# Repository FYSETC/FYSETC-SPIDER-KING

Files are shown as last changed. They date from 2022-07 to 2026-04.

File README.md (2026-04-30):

# FYSETC-SPIDER-KING

## 1. Product introduction

10 axis industrial grade 3D printer motherboard

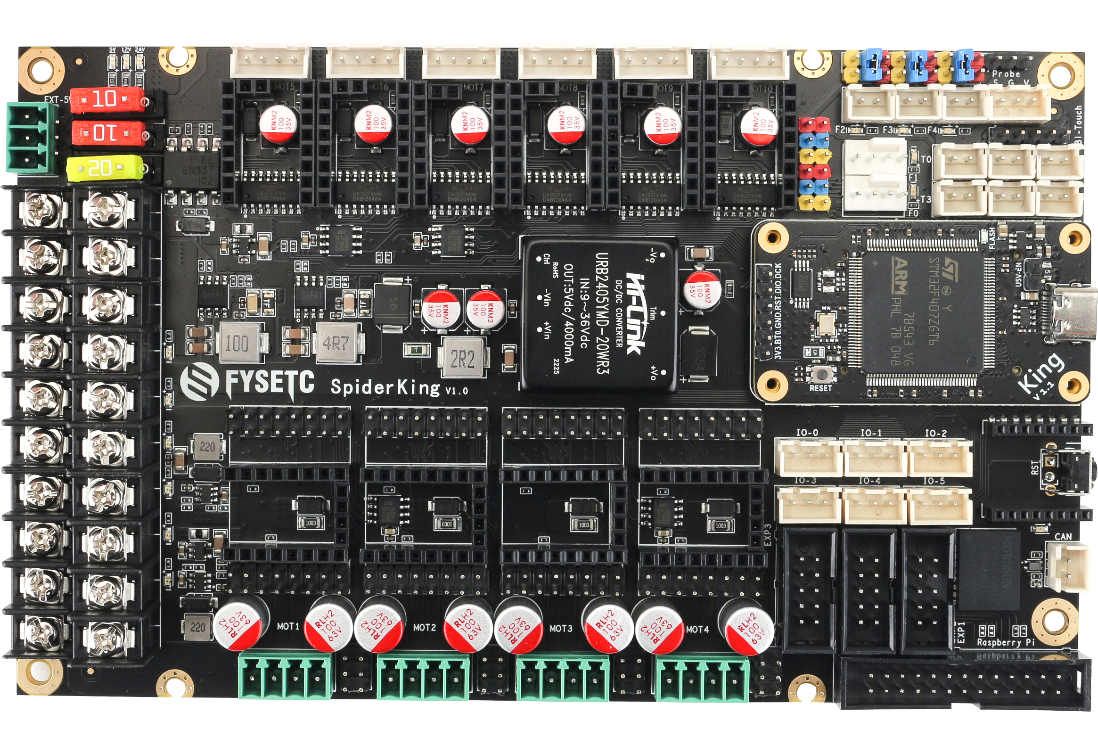
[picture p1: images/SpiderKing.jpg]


### 1.1 Advantage

1. Replaceable control core:
   It has a replaceable control core(Named 'King' core).You can freely choose between 4xRP2040(King-R) / STM32F446(King-446) / STM32F407(King-407) / STM32H7XX(King-H7xx), and even you can make your own control core(We will open source the interface).

2. Intelligent identification of stepper driver type:
   With an additional MCU, Spider-King can identify the driver type and switch the SPI/UART channel automatically.
   This feature save you time on searching doc of how to set the jumppers, keep you away from borning setting jumppers. No longer has problems with stepper driver setting. (If you want to use this feature, you need our new stepper driver)

3. Multiple firmware support:
   It supports multiple firmwares.You can choose to use Klipper / Marlin 2.0 / Reprap Firmware / GRBL and other firmware according to your preferences and needs.

4. Industrial-grade standard design, 5000V full IO isolation:
   It provides a more secure hardware base: equiped with onboard high-power isolated power supply, and the control core is isolated from all high-voltage peripherals, including stepper motor drive, MOSFET output, high-voltage input signal, CAN bus, etc.

5. 10 way stepper motor drive support:
   Onboard 10 way stepping motor drive socket, 6x 3A max (maximum 35V), 4x 6A max (maximum 55V). Any socket supports SPI / UART / standalone mode.It has a new 6A drive design. It can drive 57 or even 86 step motors without external drive;

6. A variety of communication interfaces support:
   It supports onboard 5000V isolated CAN interface, supports wireless WI-FI interface, supports ESP32 high-speed communication module, supports multiple connection to Raspberry Pi, including UART, SPI and USB.

7. Centralized heat dissipation of heat-generating components:
   We centralized most heating components like 5V power supply, stepper driver in the middle area of the board, this area can be covered with the 12CM fan for cooling. You don't need to rack your brains to design the air duct, you can get better and more stable output performance.

8. Compatible with RRF firmware standard socket design:
   The socket layout is set according to Duet wiring and layout, which is more convenient to use the RRF. And more, we adds two DUET type fan ports which have feedback signal.

9. All Solid Capacitors: Power Section：
   It can provide more stable power supply and higher efficiency.

10. Compact Design:
    It has a very small size of 177mm*108mm, realizes multiple MOSFET outputs, and supports up to 10 stepper drivers.

## 2. Documents

Check our wiki [FYSETC SPIDER KING - FYSETC WIKI](https://wiki.fysetc.com/docs/FYSETCSPIDERKING).

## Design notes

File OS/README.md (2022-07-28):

# OS

## SAMFi-OS_OrangePi_zero

Before you use the [SAMF-OS_OrangePi_zero](https://github.com/FYSETC/FYSETC-SAMFi-OS). You need an TF card with at least 8G capacity. 

### Step 1

Download and flash the OS image with `balenaEtcher` software to your TF card. Insert your flashed TF card to OrangePi-zero and connect Ethernet cable then power on. Find the ip address of OrangePi-zero on your router, host name is `orangepizero`.

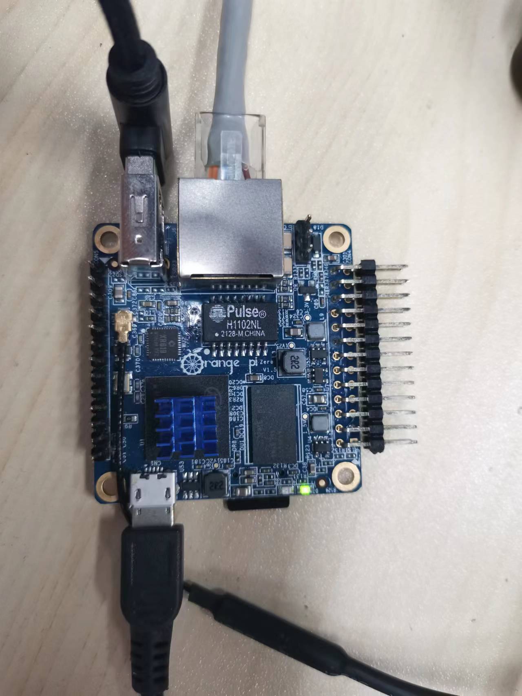
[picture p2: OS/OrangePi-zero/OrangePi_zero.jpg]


### Step 2

You can find the firmware `klipper.bin` in `OrangePi-zero` folder after you download the github repository. It is also stay in the OS path `firmwares\spider-king407.bin` after you login the OS with SSH.

Original SSH account and password:

```
account: fysetc
password: fysetc123
```

Enter DFU mode(set a jumper on `3.3V` and `BT0` pin on king core board and click the reset button, you need power on the board with 24v ), and flash the firmware with the command below after you connect your OrangePi and Spider-king with USB cable.

```
dfu-util -R -a 0 -s 0x08008000:leave -D firmwares/spider-king407.bin
```

or follow the instructions [here](https://github.com/FYSETC/FYSETC-SPIDER#44--firmware-upload) for firmware uploading. Remember to remove the `3.3v` `BT0` jumper and click the reset button after you flashed the firmware. 

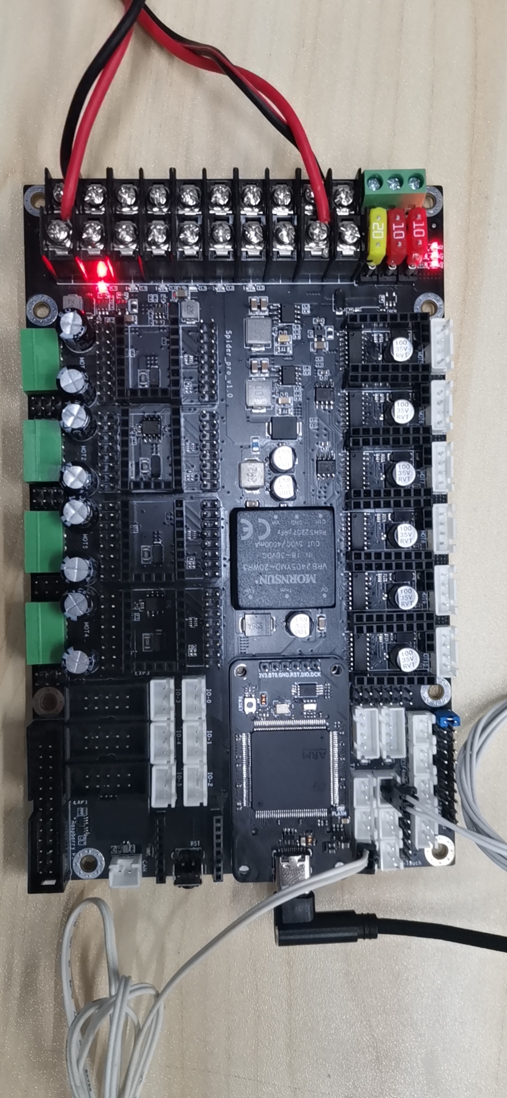
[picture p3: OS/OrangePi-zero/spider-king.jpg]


### Step 3:

Prepare the `pinter.cfg`, using the command below

```
cp klipper_config/spider-king.cfg klipper_config/printer.cfg
```

You probably need to change `id` by `ls /dev/serial/by-id` command.

I use the voron2.4 config for this example, you need to change it according to your machine. Now visit the webpage with your orangepi-zero IP address. Good to go.

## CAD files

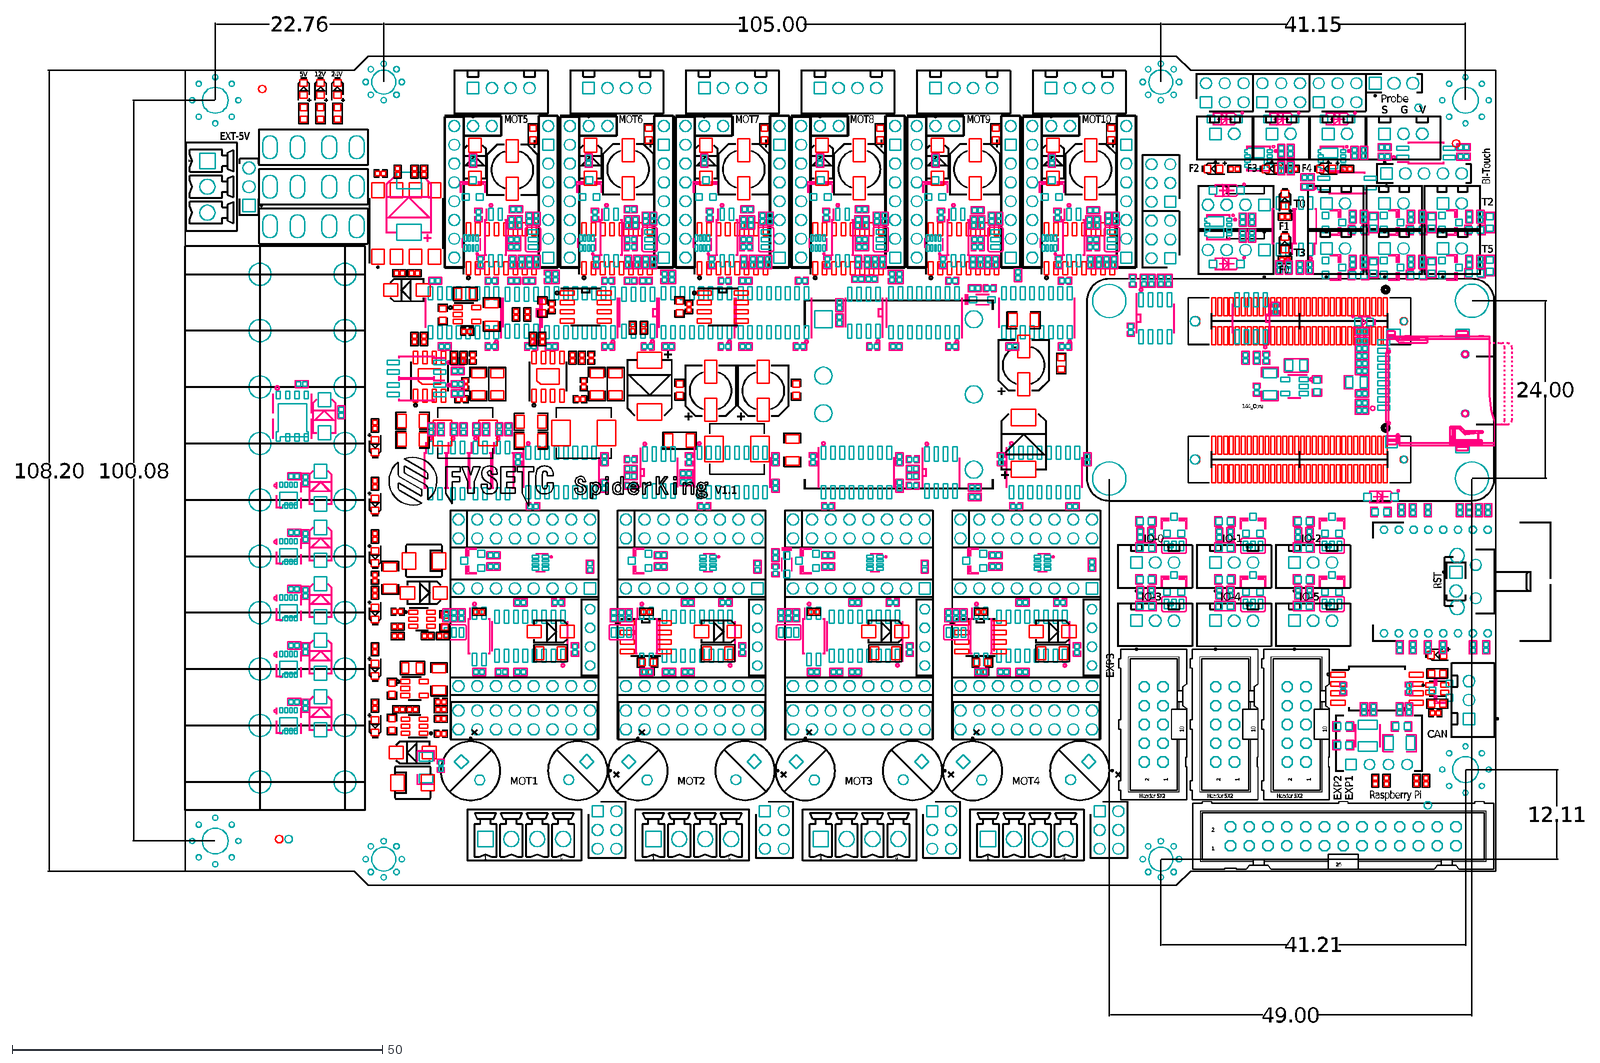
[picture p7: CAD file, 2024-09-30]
hardware/Spider_King v1.1_CAD.dxf
144_Core
1
4
26
2
10
Header 5X2
V1.1
EXT-5V
V
S
G
Probe
24V
12V
5V
RST
Bl-Touch
F4
F3
F2
F1
F0
Raspberry Pi
IO-0
T5
T3
T2
T0
IO-5
IO-4
IO-3
IO-2
IO-1
CAN
EXP2
EXP1
EXP3
MOT10
MOT9
MOT8
MOT7
MOT6
MOT5
MOT4
MOT3
MOT2
MOT1
100.08
108.20
105.00
41.15
24.00
22.76
12.11
41.21
49.00

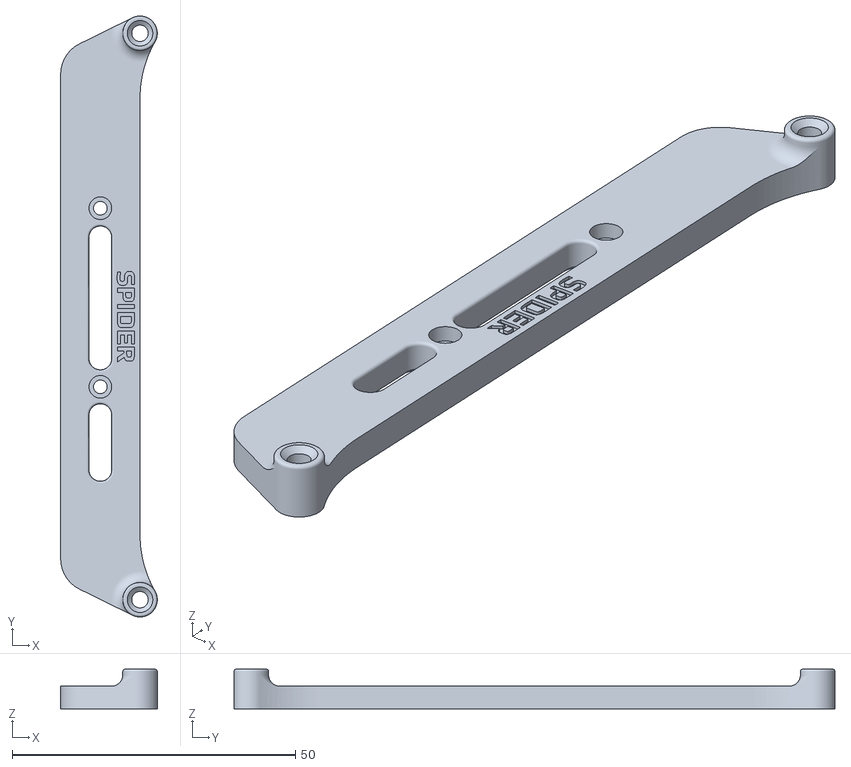
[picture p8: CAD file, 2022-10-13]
STLs/Holder_long_right.STL
17.1 x 106.0 x 7.00

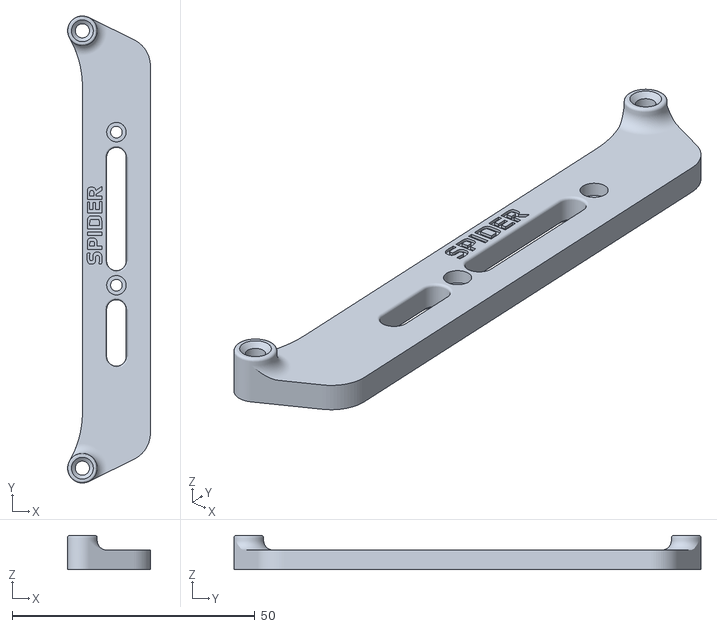
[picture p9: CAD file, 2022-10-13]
STLs/Holder_short_left.STL
17.1 x 96.1 x 7.00

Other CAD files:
hardware/Spider_King_CAD.dxf

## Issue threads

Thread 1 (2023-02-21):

TMC5160 Drivers Not detected

benagricola, 2023-02-21:
Using the example Klipper configs, as well as RRF, my SPIDER KING won't detect the BIG-5160 drivers I have installed in my board.

Klipper reports:

```
INFO:root:TMC stepper_x failed to init: Unable to write tmc spi 'stepper_x' register GLOBALSCALER
INFO:root:TMC stepper_y failed to init: Unable to write tmc spi 'stepper_y' register GLOBALSCALER
INFO:root:TMC stepper_z failed to init: Unable to write tmc spi 'stepper_z' register GLOBALSCALER
```

And RRF reports all drivers not present.

Additionally, the example Klipper configuration pins don't match the Pinout diagram in this repo, so I have no idea which pins are the correct ones.

The example Klipper config I'm using is this (using the pin layout from the PDF file in this repo).

```
[mcu]
serial: /dev/serial/by-id/usb-Klipper_stm32f407xx_260035001147393532373434-if00
restart_method: command

[stepper_x]
step_pin: PG7
dir_pin: PG6
enable_pin: PE11
rotation_distance: 40
microsteps: 16
full_steps_per_rotation:200
endstop_pin: tmc5160_stepper_x:virtual_endstop
position_min: 0
position_endstop: 0
position_max: 235
homing_speed: 35
homing_retract_dist: 5
#homing_positive_dir: true

[tmc5160 stepper_x]
## Soft SPI
spi_software_mosi_pin: PE14
spi_software_miso_pin: PE13
spi_software_sclk_pin: PE12
cs_pin: PD2
diag0_pin: !PF6
interpolate: False
run_current: 0.8
#hold_current: 0.5
stealthchop_threshold: 0
sense_resistor: 0.075
driver_SGT: 1

[stepper_y]
step_pin: PG14
dir_pin: PG12
enable_pin: PG15
microsteps: 16
rotation_distance: 40
full_steps_per_rotation: 200
endstop_pin: tmc5160_stepper_y:virtual_endstop
position_min: 0
position_endstop: 0
position_max: 235
homing_speed: 35
homing_retract_dist: 5

[tmc5160 stepper_y]
## Soft SPI
spi_software_mosi_pin: PE14
spi_software_miso_pin: PE13
spi_software_sclk_pin: PE12
cs_pin: PD8
diag0_pin: !PF8
interpolate: False   #true   False
run_current: 0.8
#hold_current: 0.5
stealthchop_threshold: 0
sense_resistor: 0.075
driver_SGT: 1

#####################################################################
#   Z Motor
#####################################################################

[stepper_z]
step_pin: PD4
dir_pin: PD6
enable_pin: PD5
rotation_distance: 8
gear_ratio: 40:16
microsteps: 256
endstop_pin: tmc5160_stepper_z:virtual_endstop
position_endstop: 0
position_max: 235
position_min: 0
homing_speed: 7
second_homing_speed: 3
homing_retract_dist: 3

[tmc5160 stepper_z]
spi_software_mosi_pin: PE14
spi_software_miso_pin: PE13
spi_software_sclk_pin: PE12
cs_pin: PD7
diag0_pin: !PF11
interpolate: False   #true
run_current: 0.7
hold_current: 0.4
sense_resistor: 0.110
stealthchop_threshold: 0

[printer]
kinematics: cartesian
max_velocity: 200
max_accel: 1500
max_z_velocity: 10
max_z_accel: 100
square_corner_velocity: 4.0
```

Big5160 boards are installed in the orientation from the WIKI - With the BIG-5160 text upside-down when looking at the board from the high voltage motor connectors.

Please help work out what's wrong here, because the board won't work without drivers :)

benagricola, 2023-02-22:
For anyone else finding this:

The BIG5160 drivers specifically need power on the `48V-PWR` rail _as well as_ whatever you have on `PWE-IN`. You can run 24v to both of these and the drivers will work fine, but you have to have _both_ connected up, as `PWE-IN` does not provider power to the "High Voltage" motor drivers.

The configuration which worked great for me with standard currents (not tuned yet) is:

```
[mcu]
serial: /dev/serial/by-id/usb-Klipper_stm32f407xx_260035001147393532373434-if00
restart_method: command

[stepper_x]
step_pin: PG7
dir_pin: PG6
enable_pin: !PE11
microsteps: 16
rotation_distance: 40
full_steps_per_rotation: 200
endstop_pin: !PC5
position_min: 0
position_endstop: 0
position_max: 235
homing_speed: 35
homing_retract_dist: 5

[tmc5160 stepper_x]
## Soft SPI
spi_software_mosi_pin: PE14
spi_software_miso_pin: PE13
spi_software_sclk_pin: PE12
cs_pin: PD2
diag1_pin: PF6
interpolate: False   #true   False
run_current: 0.8
#hold_current: 0.5
stealthchop_threshold: 0
sense_resistor: 0.075
driver_SGT: -64

[stepper_y]
step_pin: PG14
dir_pin: PG12
enable_pin: !PG15
microsteps: 16
rotation_distance: 40
full_steps_per_rotation: 200
endstop_pin: !PC4
position_min: 0
position_endstop: 0
position_max: 235
homing_speed: 35
homing_retract_dist: 5

[tmc5160 stepper_y]
## Soft SPI
spi_software_mosi_pin: PE14
spi_software_miso_pin: PE13
spi_software_sclk_pin: PE12
cs_pin: PD8
diag1_pin: PF8
interpolate: False   #true   False
run_current: 0.8
#hold_current: 0.5
stealthchop_threshold: 0
sense_resistor: 0.075
driver_SGT: -64

#####################################################################
#   Z Motor
#####################################################################

[stepper_z]
step_pin: PD4
dir_pin: PD6
enable_pin: !PD5
rotation_distance: 8
gear_ratio: 40:16
microsteps: 256
endstop_pin: !PB6
position_endstop: 0
position_max: 235
position_min: 0
homing_speed: 7
second_homing_speed: 3
homing_retract_dist: 3

[tmc5160 stepper_z]
spi_software_mosi_pin: PE14
spi_software_miso_pin: PE13
spi_software_sclk_pin: PE12
cs_pin: PD7
diag1_pin: PF11
interpolate: False   #true
run_current: 0.7
hold_current: 0.4
sense_resistor: 0.075
stealthchop_threshold: 0
sense_resistor: 0.075
driver_SGT: -64

[printer]
kinematics: cartesian
max_velocity: 200
max_accel: 1500
max_z_velocity: 10
max_z_accel: 100

[display_status]
[pause_resume]
[virtual_sdcard]
path = /home/bagricola/klipper/blah

[board_pins]
aliases:
    # EXP1 header
    EXP1_1=PC9, EXP1_3=PC12, EXP1_5=PC10, EXP1_7=PG4, EXP1_9=<GND>,
    EXP1_2=PA8, EXP1_4=PD0, EXP1_6=PC11, EXP1_8=PE7, EXP1_10=<5V>,
    # EXP2 header
    EXP2_1=PA6, EXP2_3=PC6, EXP2_5=PC7, EXP2_7=PB10,  EXP2_9=<GND>,
    EXP2_2=PA5, EXP2_4=PA4, EXP2_6=PA7, EXP2_8=<RST>, EXP2_10=<5V>,

[display]
lcd_type: uc1701
cs_pin: EXP1_3
a0_pin: EXP1_4
rst_pin: EXP1_5
contrast: 63
encoder_pins: ^EXP2_5, ^EXP2_3
click_pin: ^!EXP1_2
spi_software_miso_pin: EXP2_1
spi_software_mosi_pin: EXP2_6
spi_software_sclk_pin: EXP2_2

[output_pin beeper]
pin: EXP1_1

[neopixel fysetc_mini12864]
pin: EXP1_6
chain_count: 3
color_order: RGB
initial_RED: 0.4
initial_GREEN: 0.4
initial_BLUE: 0.4

[delayed_gcode setdisplayneopixel]
initial_duration: 1
gcode:
        SET_LED LED=fysetc_mini12864 RED=1 GREEN=1 BLUE=1 INDEX=1 TRANSMIT=0
        SET_LED LED=fysetc_mini12864 RED=1 GREEN=0 BLUE=0 INDEX=2 TRANSMIT=0
        SET_LED LED=fysetc_mini12864 RED=1 GREEN=0 BLUE=0 INDEX=3

[menu]

[gcode_button emergency_stop]
pin: !PF14
press_gcode:
    M117 "Emergency Stop Pressed!"
    SET_LED LED=fysetc_mini12864 RED=1 GREEN=0 BLUE=0 INDEX=1
    M112
```

This is using BIG5160 drivers in the 1, 2 and 4 motor positions, X,Y and Z endstops in IO0, IO1 and IO2, the LED + RGB screen plugged into `EXP1` and `EXP2`, and a normally-closed e-stop button on IO5.

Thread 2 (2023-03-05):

STM32F407 not accepting firmware.bin files or showing USB-serial connection

dmason1992, 2023-03-05:
I have been trying to get [Remora](https://github.com/scottalford75/Remora) installed on the Spider King board.

Unfortunately during my trials the board has stopped responding to firmware. I am able to connect via DFU when BT0 is jumped to 3v3 pin so I can upload new firmware via the STM32Cube programmer software.

Can you provide the standard bootloader to get it back to factory state and for firmware to work via SD card upload.

Note - possibly unrelated but the USB serial does not work right now and a device only connects to the PC when the BT0 jumper is added and the board is reset.

dmason1992, 2023-04-28:
Fixed by flashing factory firmware for STM chip via USB option

Closed 2023-04-28.

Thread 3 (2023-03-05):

Add Remora for Linux CNC support

dmason1992, 2023-03-05:
Hi,

The high current drivers on this board make it a great candidate for CNC machine control however I would like to use LinuxCNC which required Remora (https://github.com/scottalford75/Remora) to be run on the board.

Please can you add remora bin + config files?

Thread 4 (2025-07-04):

All tmc 2209 on error: Unable to read tmc uart 'stepper_z1' register GCONF

mrtian, 2025-07-04:
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

**I put my tmc 2209 to BTT ,it's work fine.**

my printer config:

## In MOT5 Position
## Z0 Stepper - Front Left
[stepper_z]
step_pin: PE5
dir_pin: PC13
enable_pin: !PE6
microsteps: 16
rotation_distance: 2 #与丝杠导程数一致
full_steps_per_rotation: 200
gear_ratio: 40:16
microsteps: 256
##  In IO-2 Position
endstop_pin: ^PB6
##  Z-position of nozzle (in mm) to z-endstop trigger point relative to print surface (Z0)
##  (+) value = endstop above Z0, (-) value = endstop below
##  Increasing position_endstop brings nozzle closer to the bed
##  After you run Z_ENDSTOP_CALIBRATE, position_endstop will be stored at the very end of your config
position_endstop: 0
position_max: 300
position_min: -3
homing_speed: 6
second_homing_speed: 3
homing_retract_dist: 3

##  Make sure to update below for your relevant driver (2208 or 2209)
[tmc2209 stepper_z]
uart_pin: PC14
uart_address: 0
interpolate: True
run_current: 0.8
hold_current: 0.5
stealthchop_threshold: 0

##  In MOT6 Position
##  Z1 Stepper Rear Center
[stepper_z1]
step_pin: PE3
dir_pin: !PE4
enable_pin: !PE2
microsteps: 16
rotation_distance: 2
full_steps_per_rotation: 200

##  Make sure to update below for your relevant driver (2208 or 2209)
[tmc2209 stepper_z1]
uart_pin: PC15
uart_address: 0
interpolate: True
run_current: 0.8
hold_current: 0.5
sense_resistor: 0.110
stealthchop_threshold: 0

##  In MOT7 Position
##  Z2 Stepper - Front Right
[stepper_z2]
step_pin: PG13
dir_pin: PG8
enable_pin: !PG9
microsteps: 16
rotation_distance: 2
full_steps_per_rotation: 200

##  Make sure to update below for your relevant driver (2208 or 2209)
[tmc2209 stepper_z2]
uart_pin: PG3
uart_address: 0
interpolate: True
run_current: 0.8
hold_current: 0.5
sense_resistor: 0.110
stealthchop_threshold: 0

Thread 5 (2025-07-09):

说好几年了，这个接口在哪里能找到？

mrtian, 2025-07-09:
Replaceable control core: It has a replaceable control core(Named 'King' core).You can freely choose between 4xRP2040(King-R) / STM32F446(King-446) / STM32F407(King-407) / STM32H7XX(King-H7xx), and even you can make your own control core(We will open source the interface).

说好几年了，这个接口在哪里能找到？

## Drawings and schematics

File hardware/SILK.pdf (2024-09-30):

# ART FILM - adt

# EXT-5V

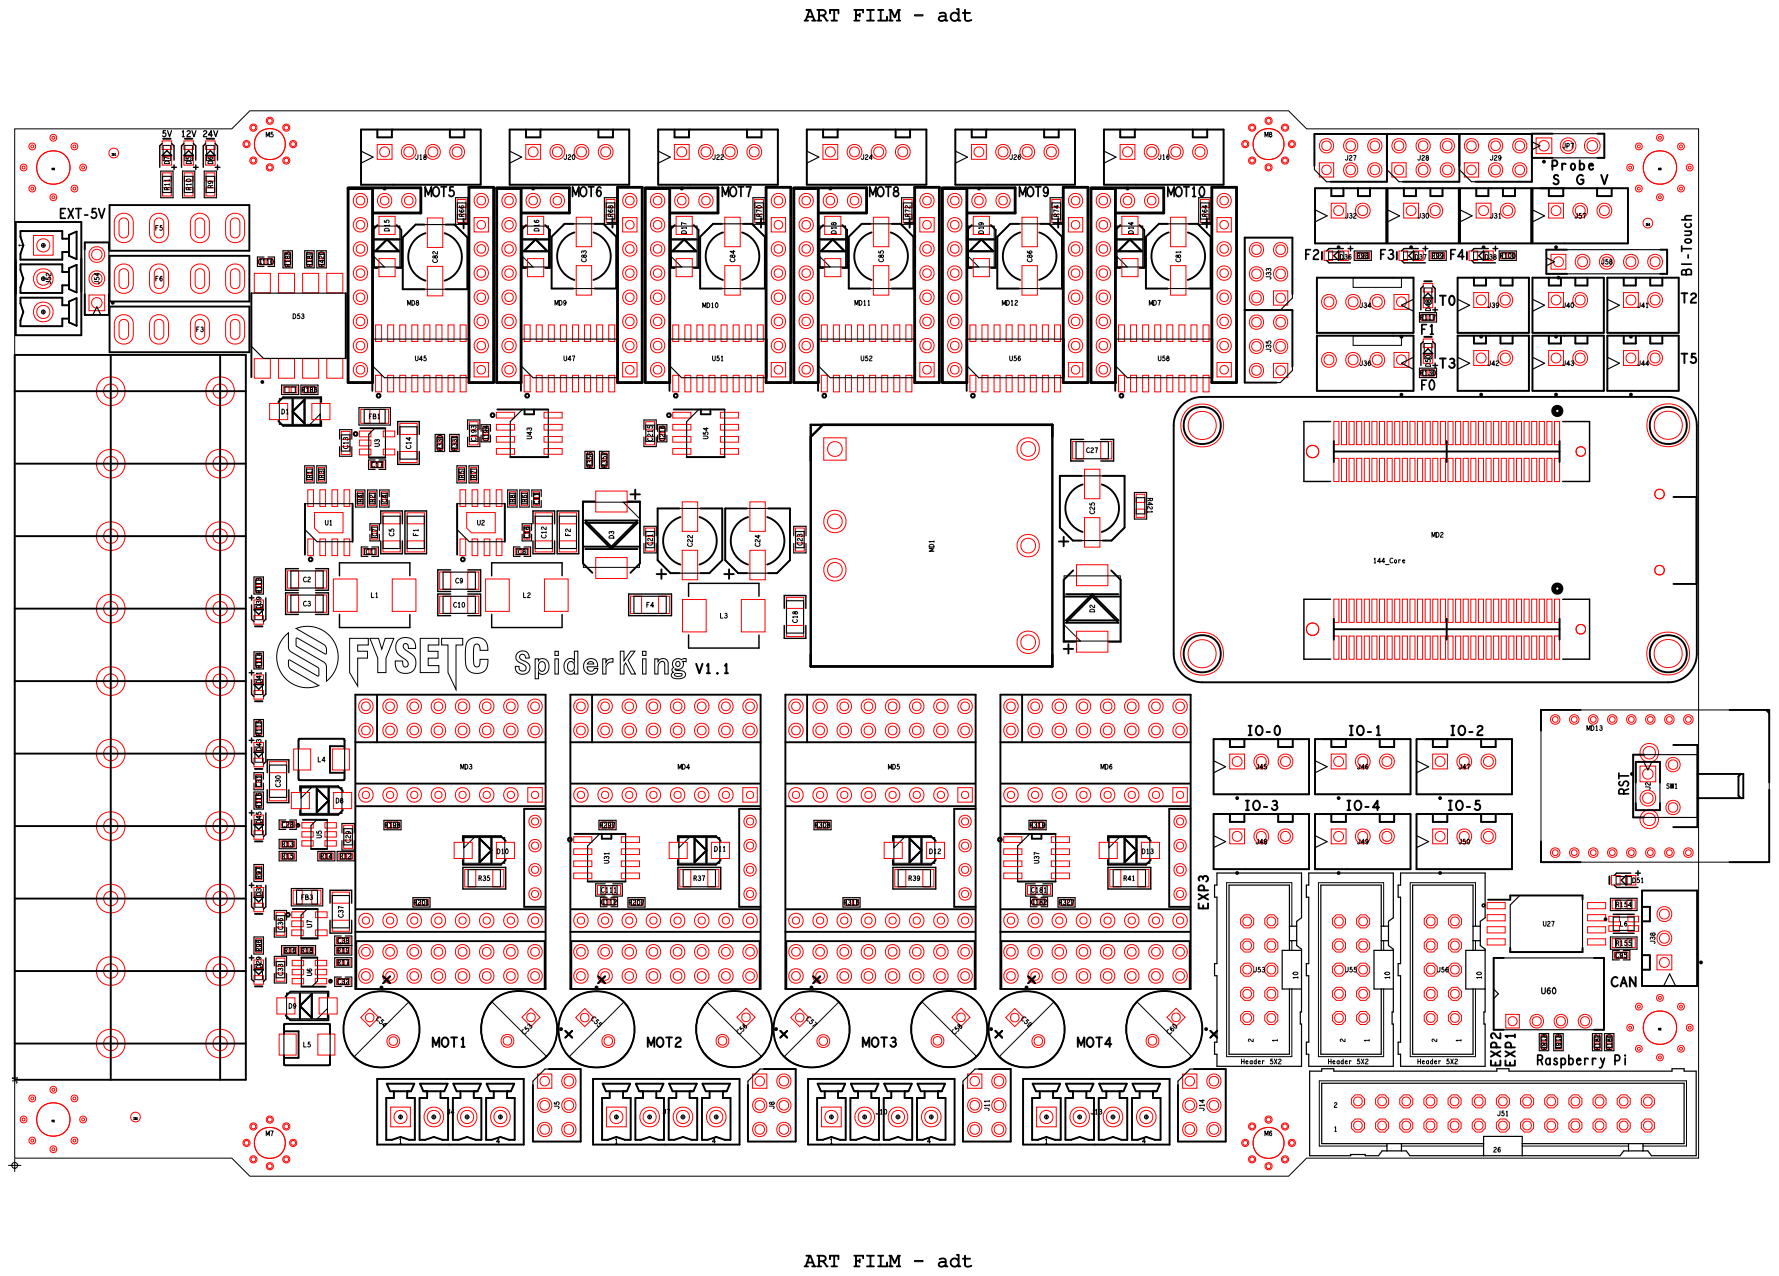
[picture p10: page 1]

# ART FILM - adb

5V

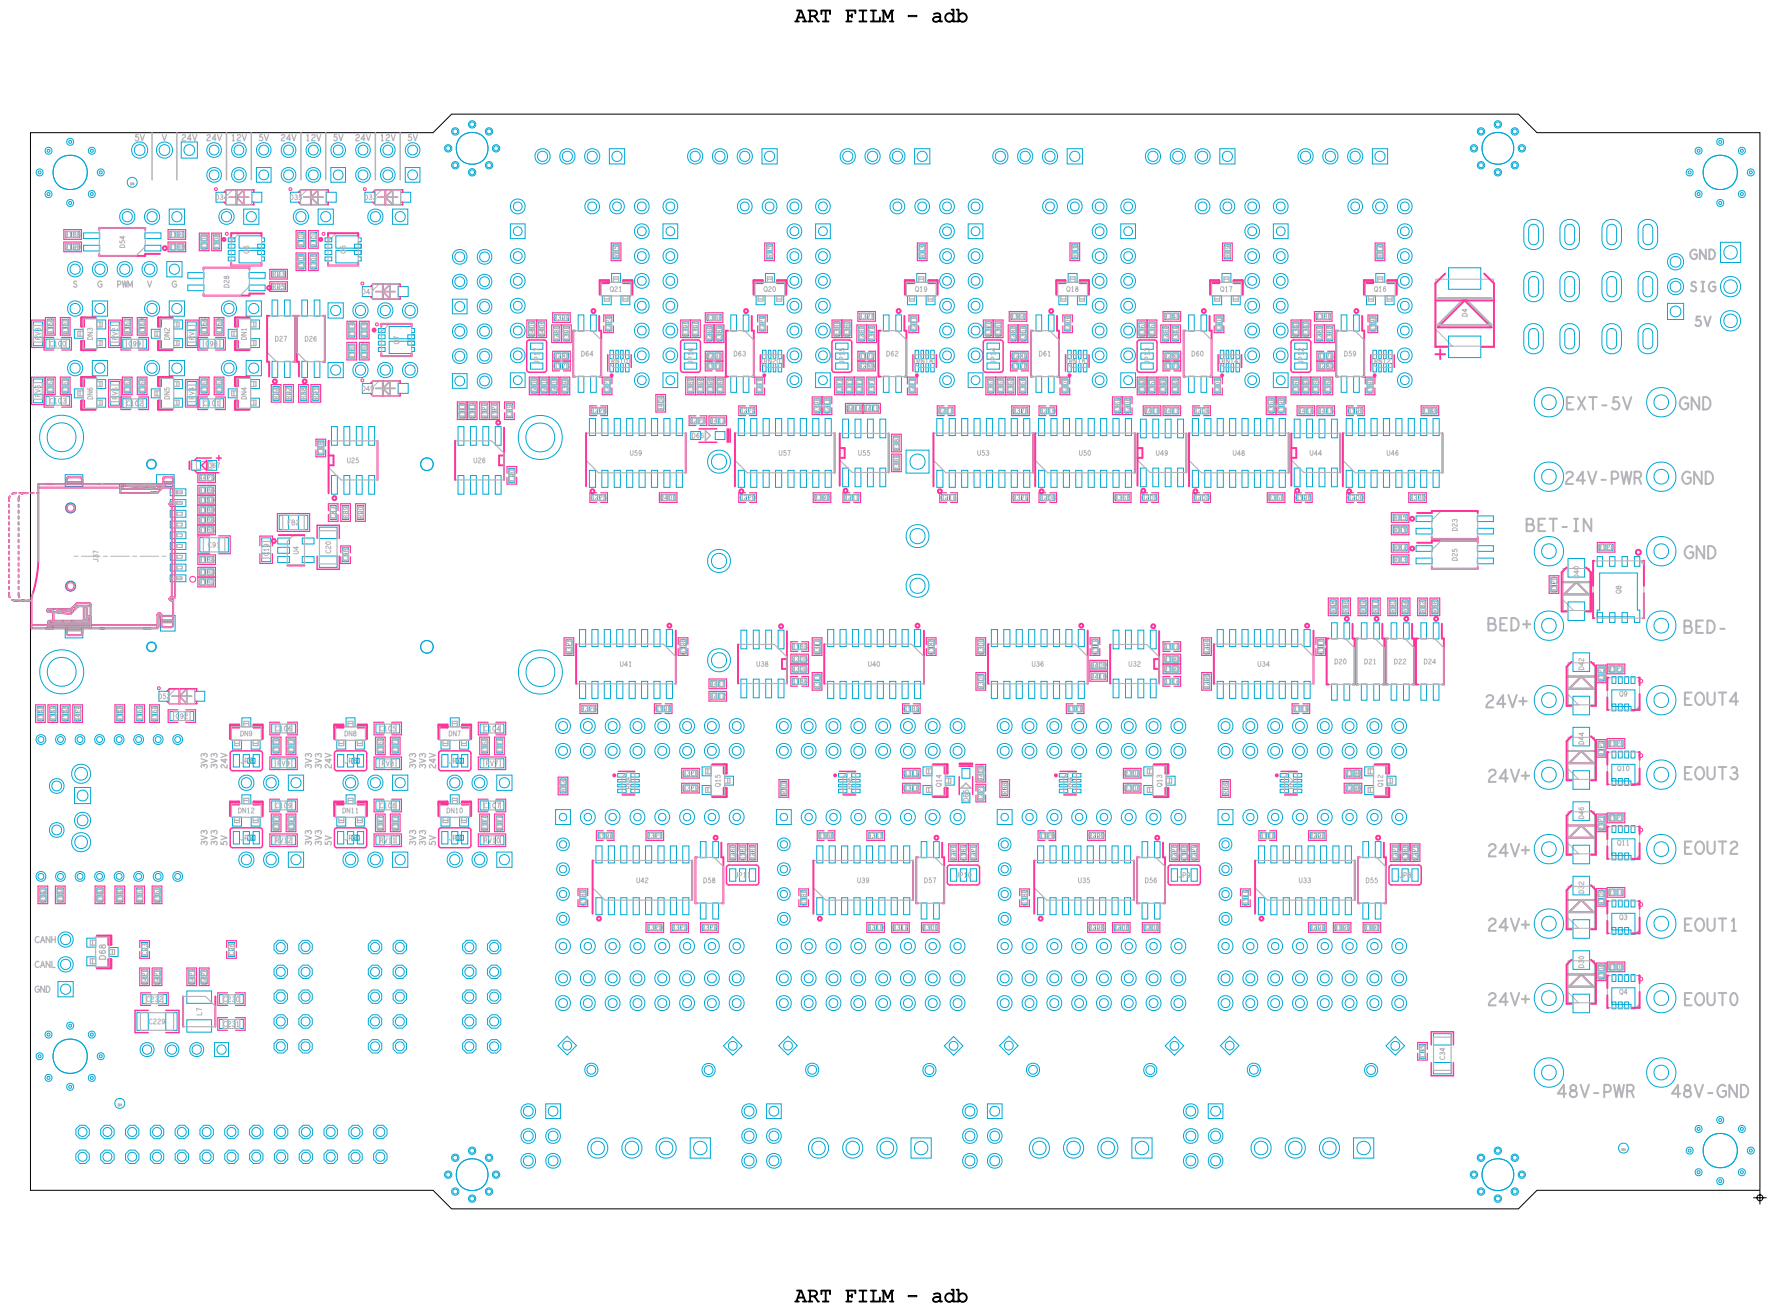
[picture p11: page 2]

# ART FILM - silktop

# EXT-5V

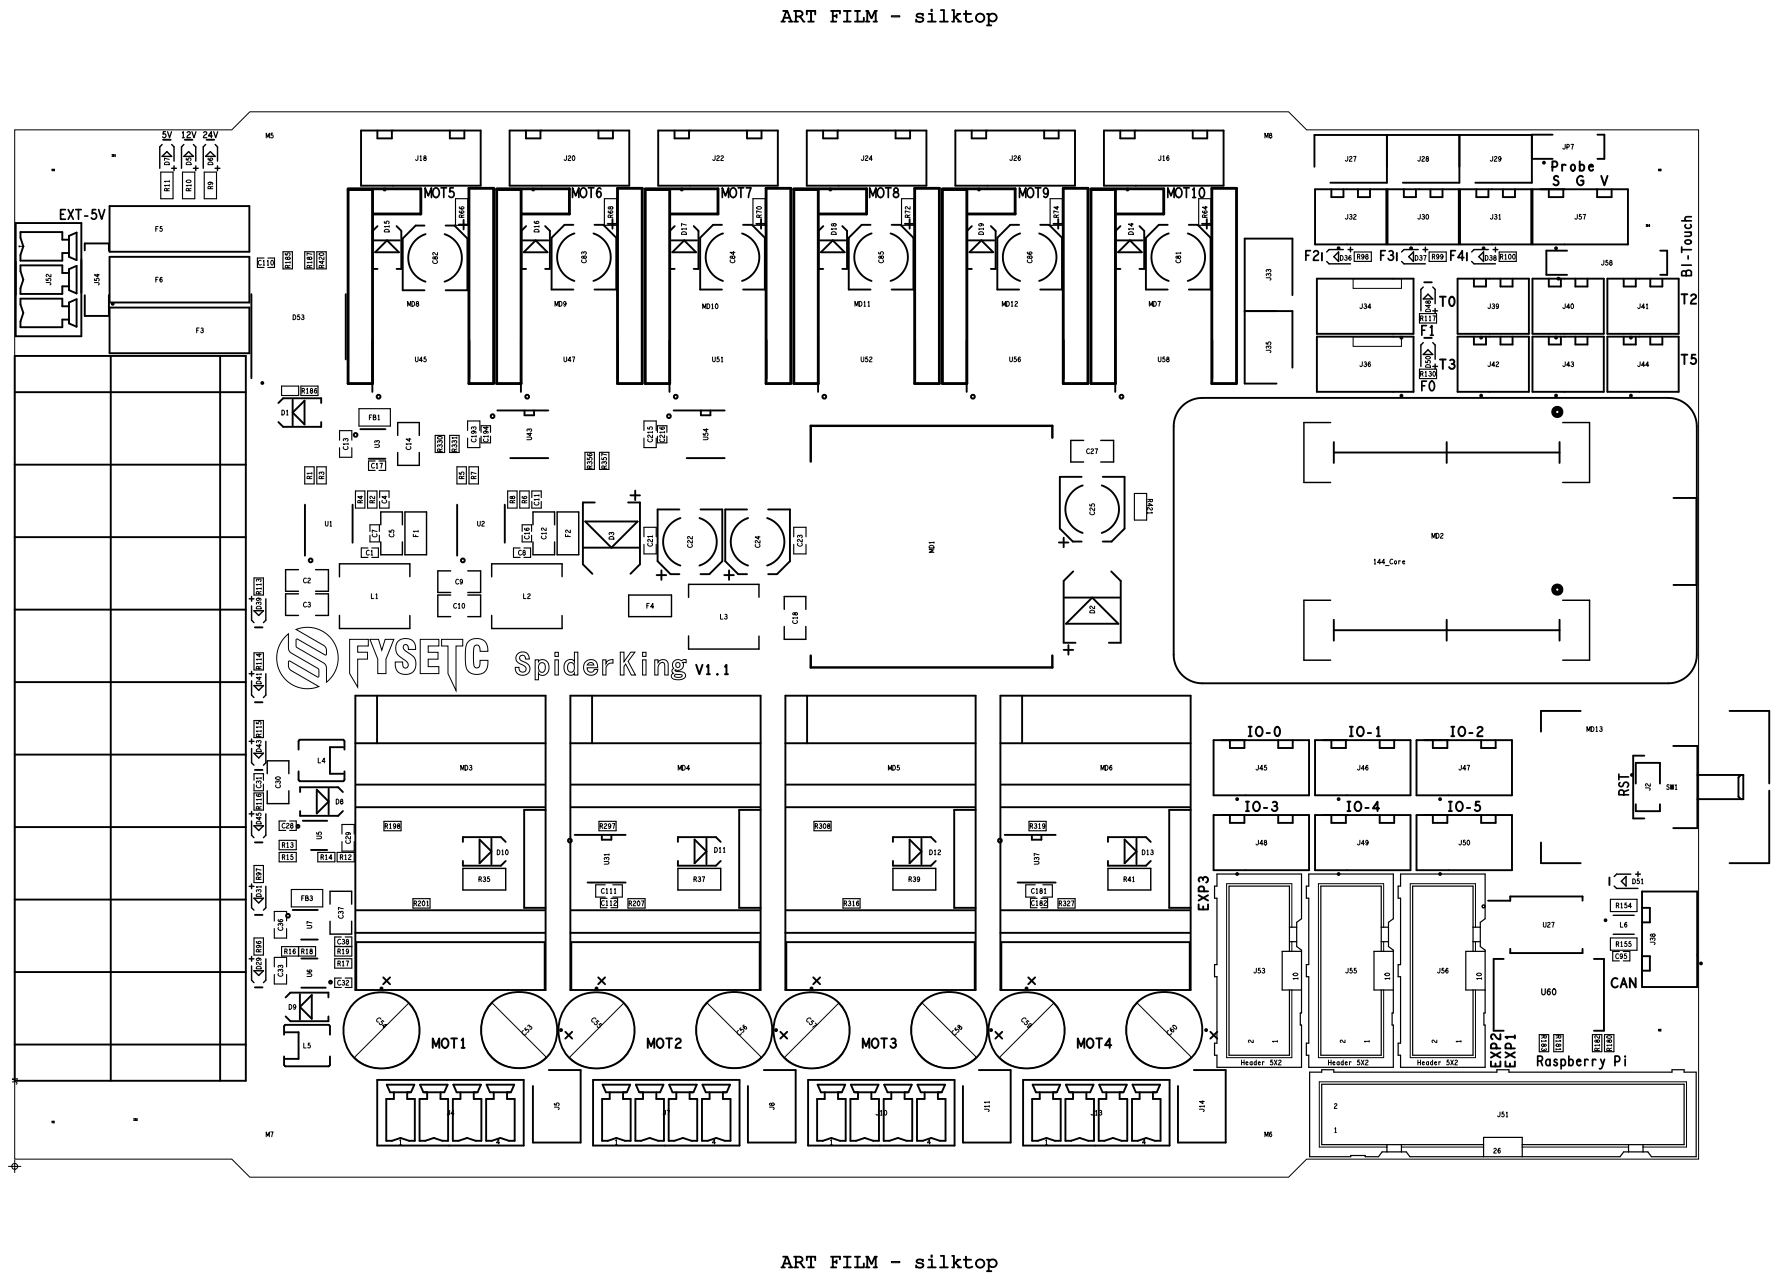
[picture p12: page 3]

# ART FILM - silkbotm

5V

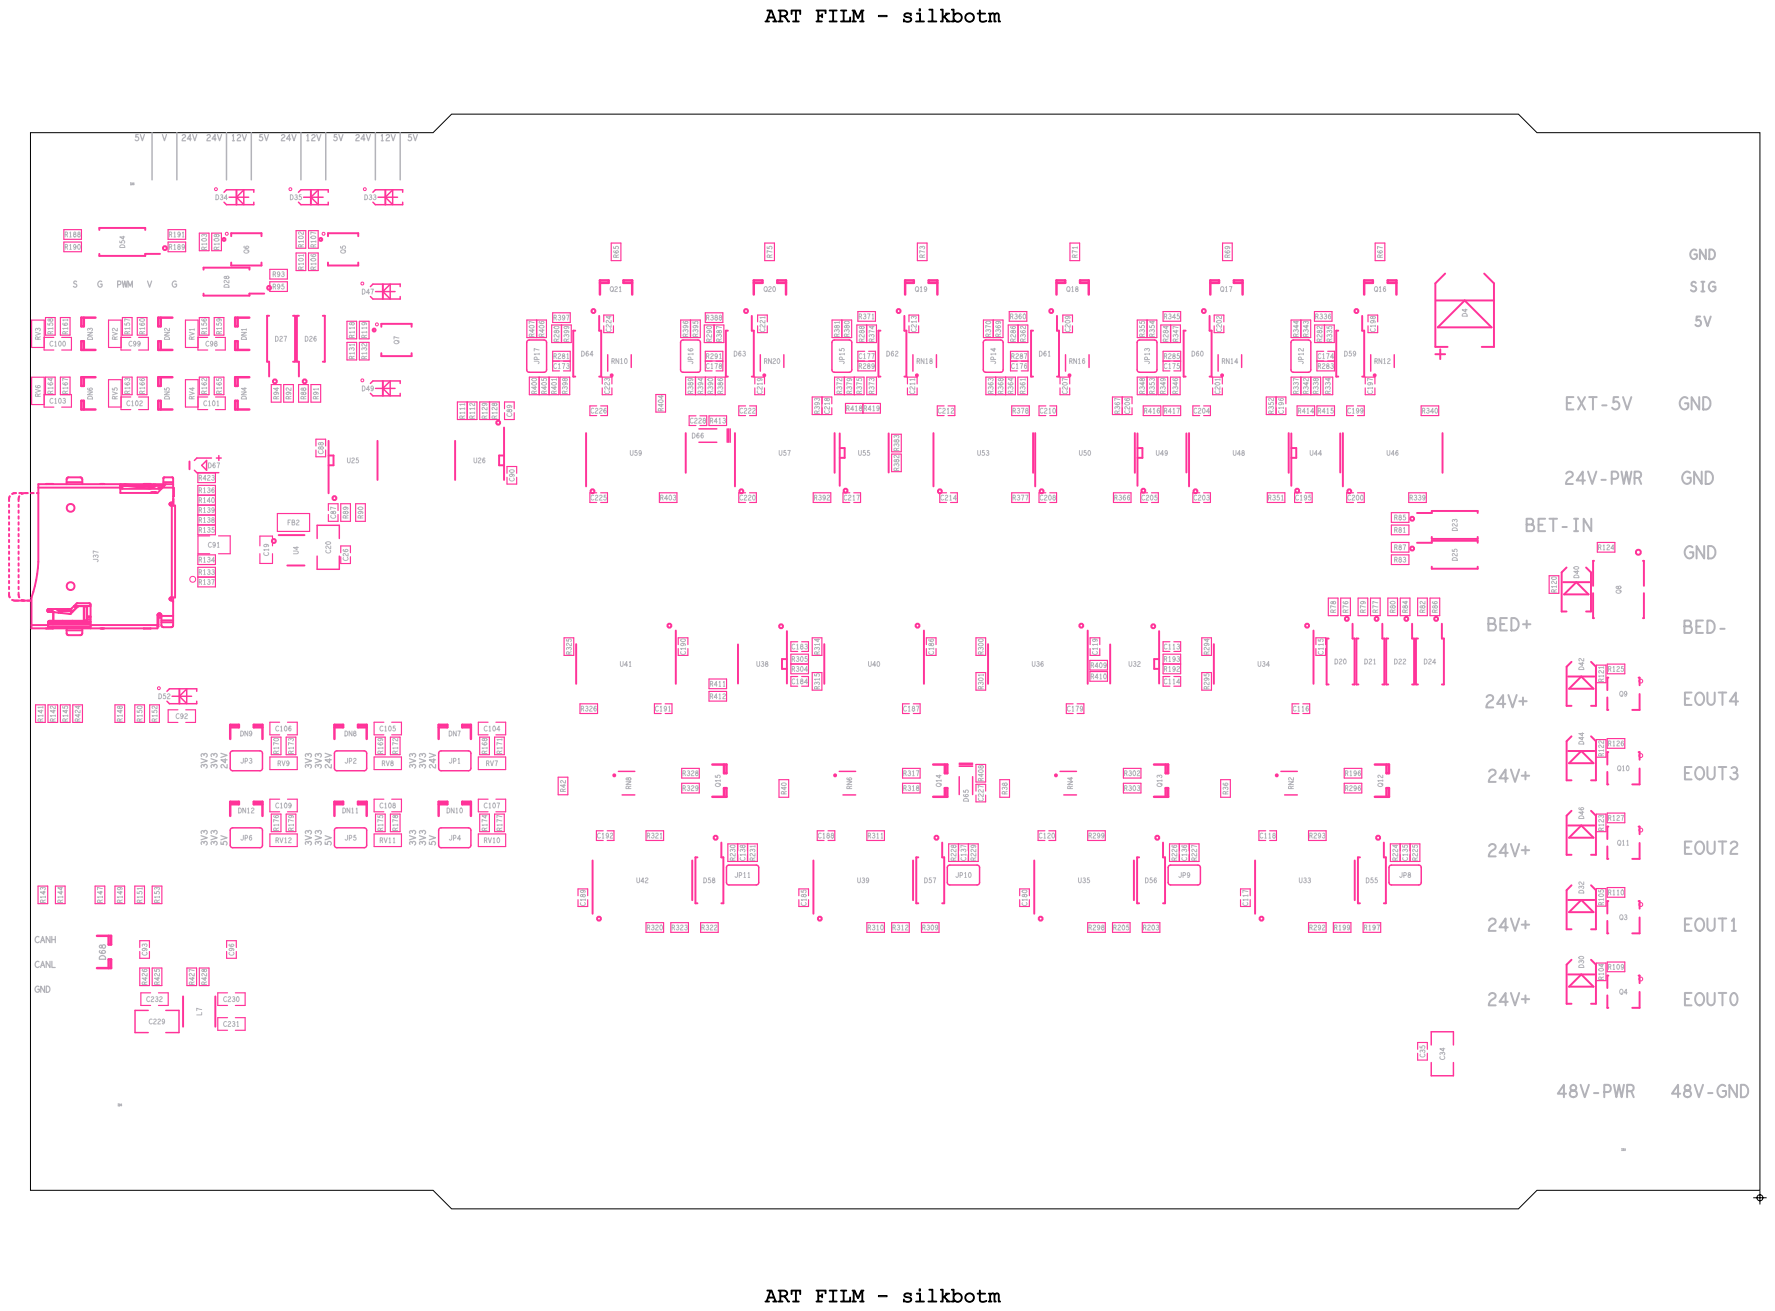
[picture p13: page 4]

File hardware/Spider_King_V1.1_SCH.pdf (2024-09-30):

24V

+12V

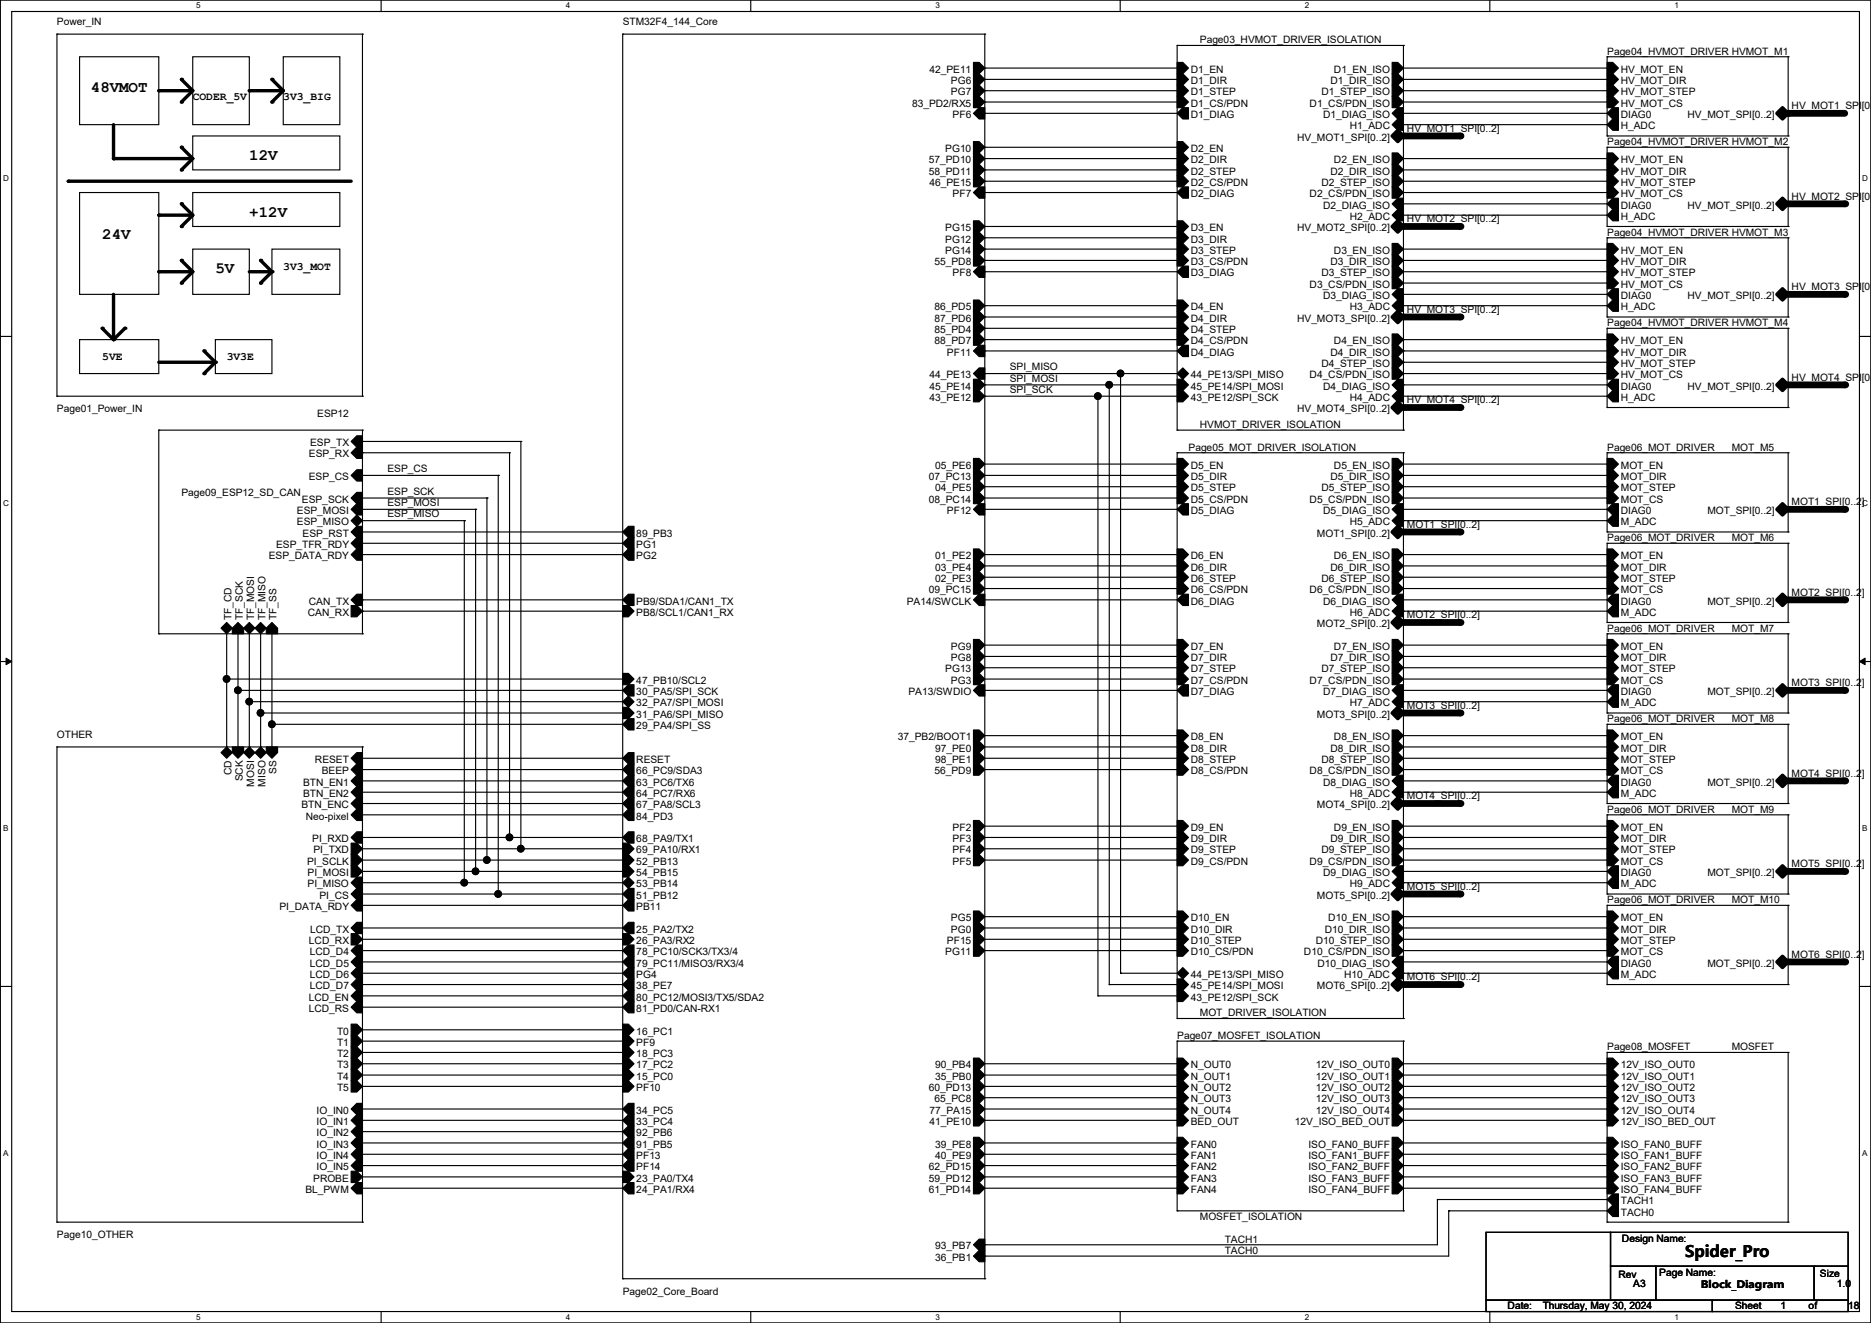
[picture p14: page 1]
3V3_MOT; 48VMOT; CODER_5V; 3V3_BIG; Design Name:; Rev; Page Name:; Size; Date:; Sheet; Spider_Pro; Thursday, May 30, 2024; Block_Diagram; HVMOT_DRIVER_ISOLATION; Page03_HVMOT_DRIVER_ISOLATION; D1_EN_ISO; D1_DIR; D1_DIR_ISO; D2_EN_ISO; D4_EN_ISO; D2_DIR; D2_DIR_ISO; D4_DIR; D4_DIR_ISO; D1_DIAG; D1_DIAG_ISO; D2_DIAG; D2_DIAG_ISO; D4_DIAG; D4_DIAG_ISO; D1_CS/PDN; D1_CS/PDN_ISO; D3_CS/PDN; D3_CS/PDN_ISO; D2_CS/PDN; D2_CS/PDN_ISO; D4_CS/PDN; D4_CS/PDN_ISO; D1_STEP; D1_STEP_ISO; D2_STEP; D2_STEP_ISO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

SPI_MOSI
SPI_SCK

5 | 4 | 3 | 2 | 1

D D

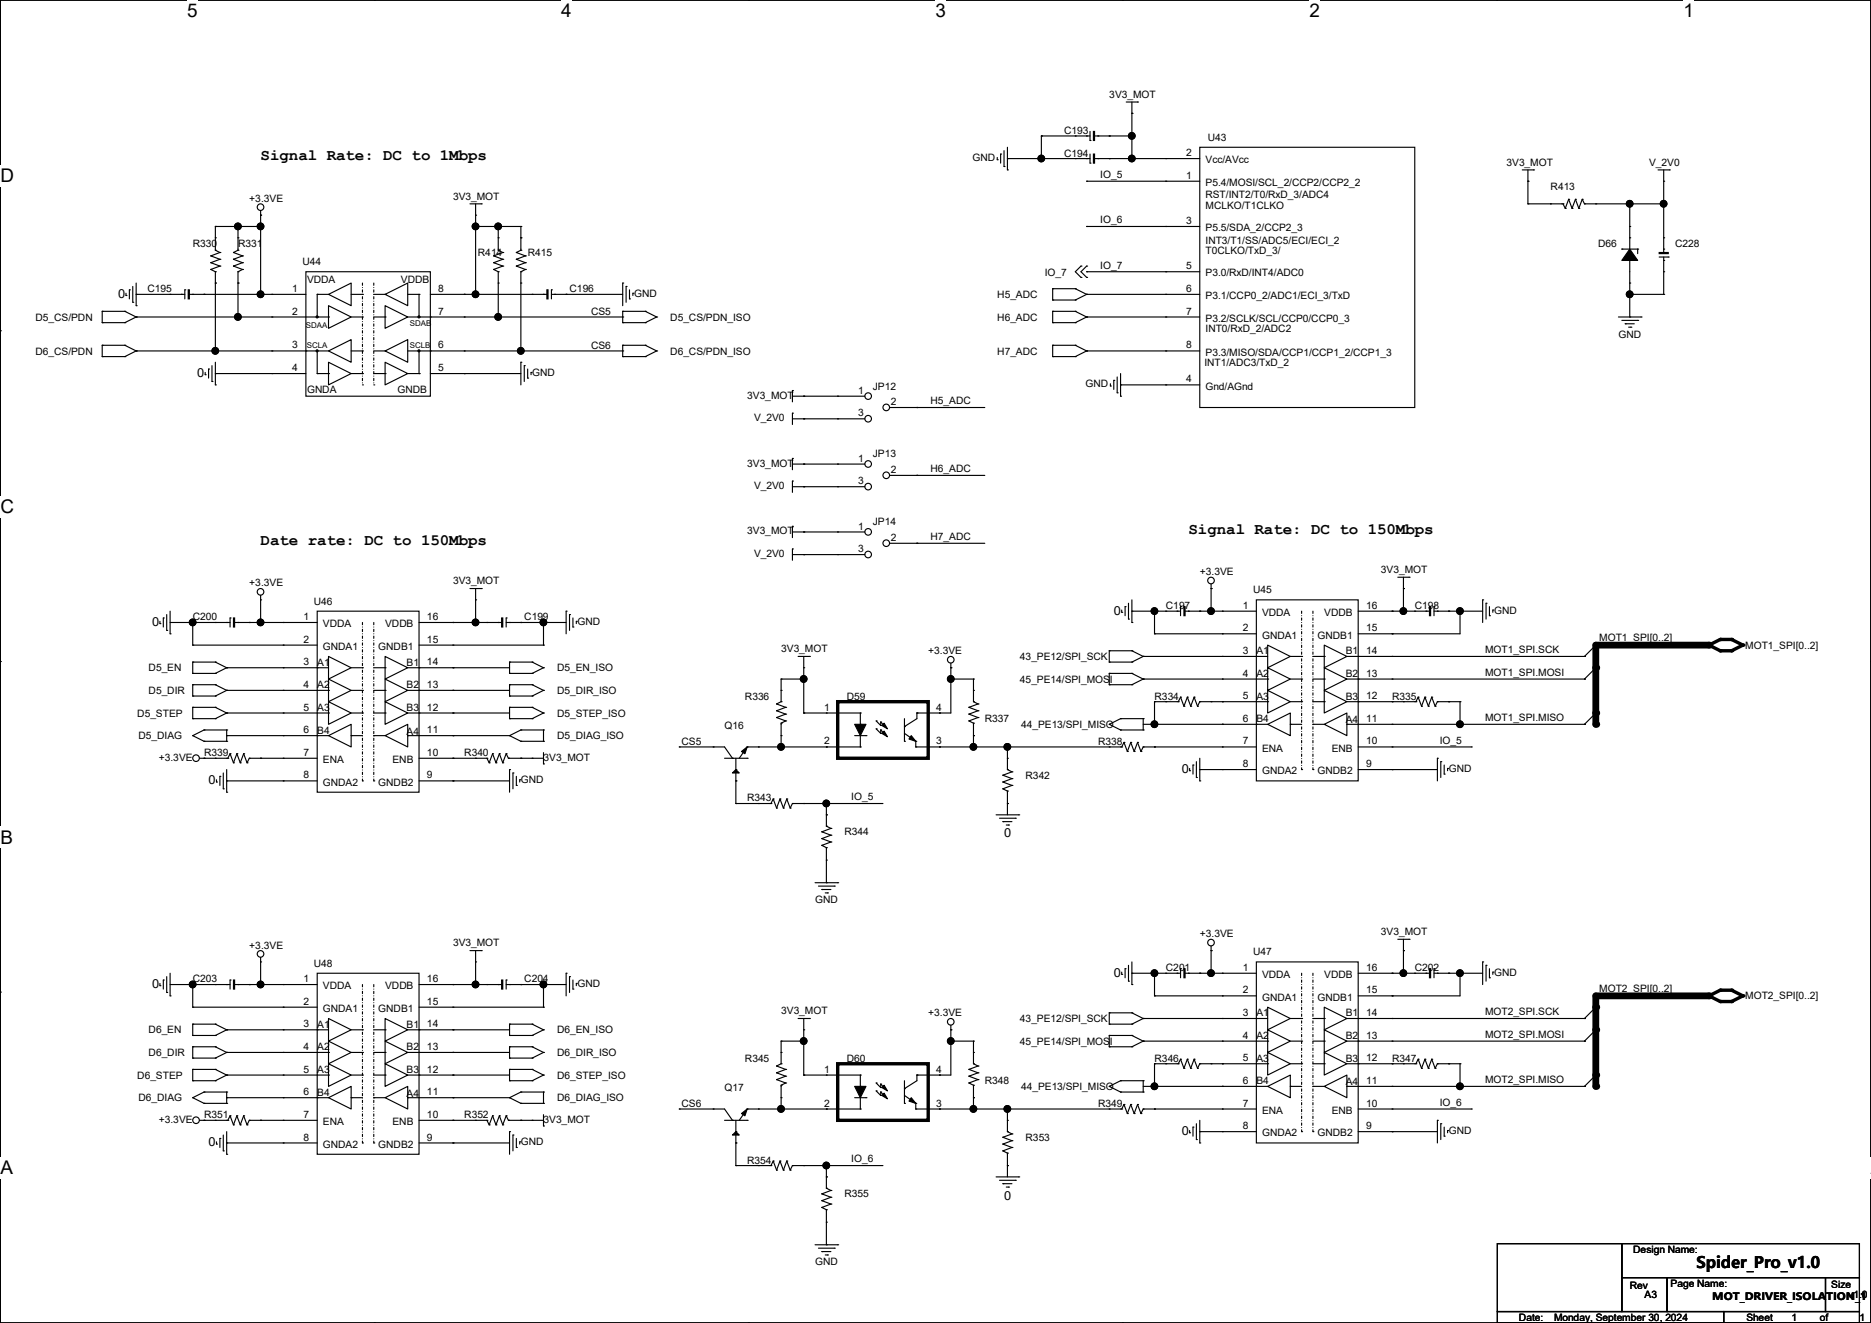
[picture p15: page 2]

Signal Rate: DC to 1Mbps

Signal Rate: DC to 150Mbps Date rate: DC to 150Mbps

D D

## Signal Rate: DC to 1Mbps

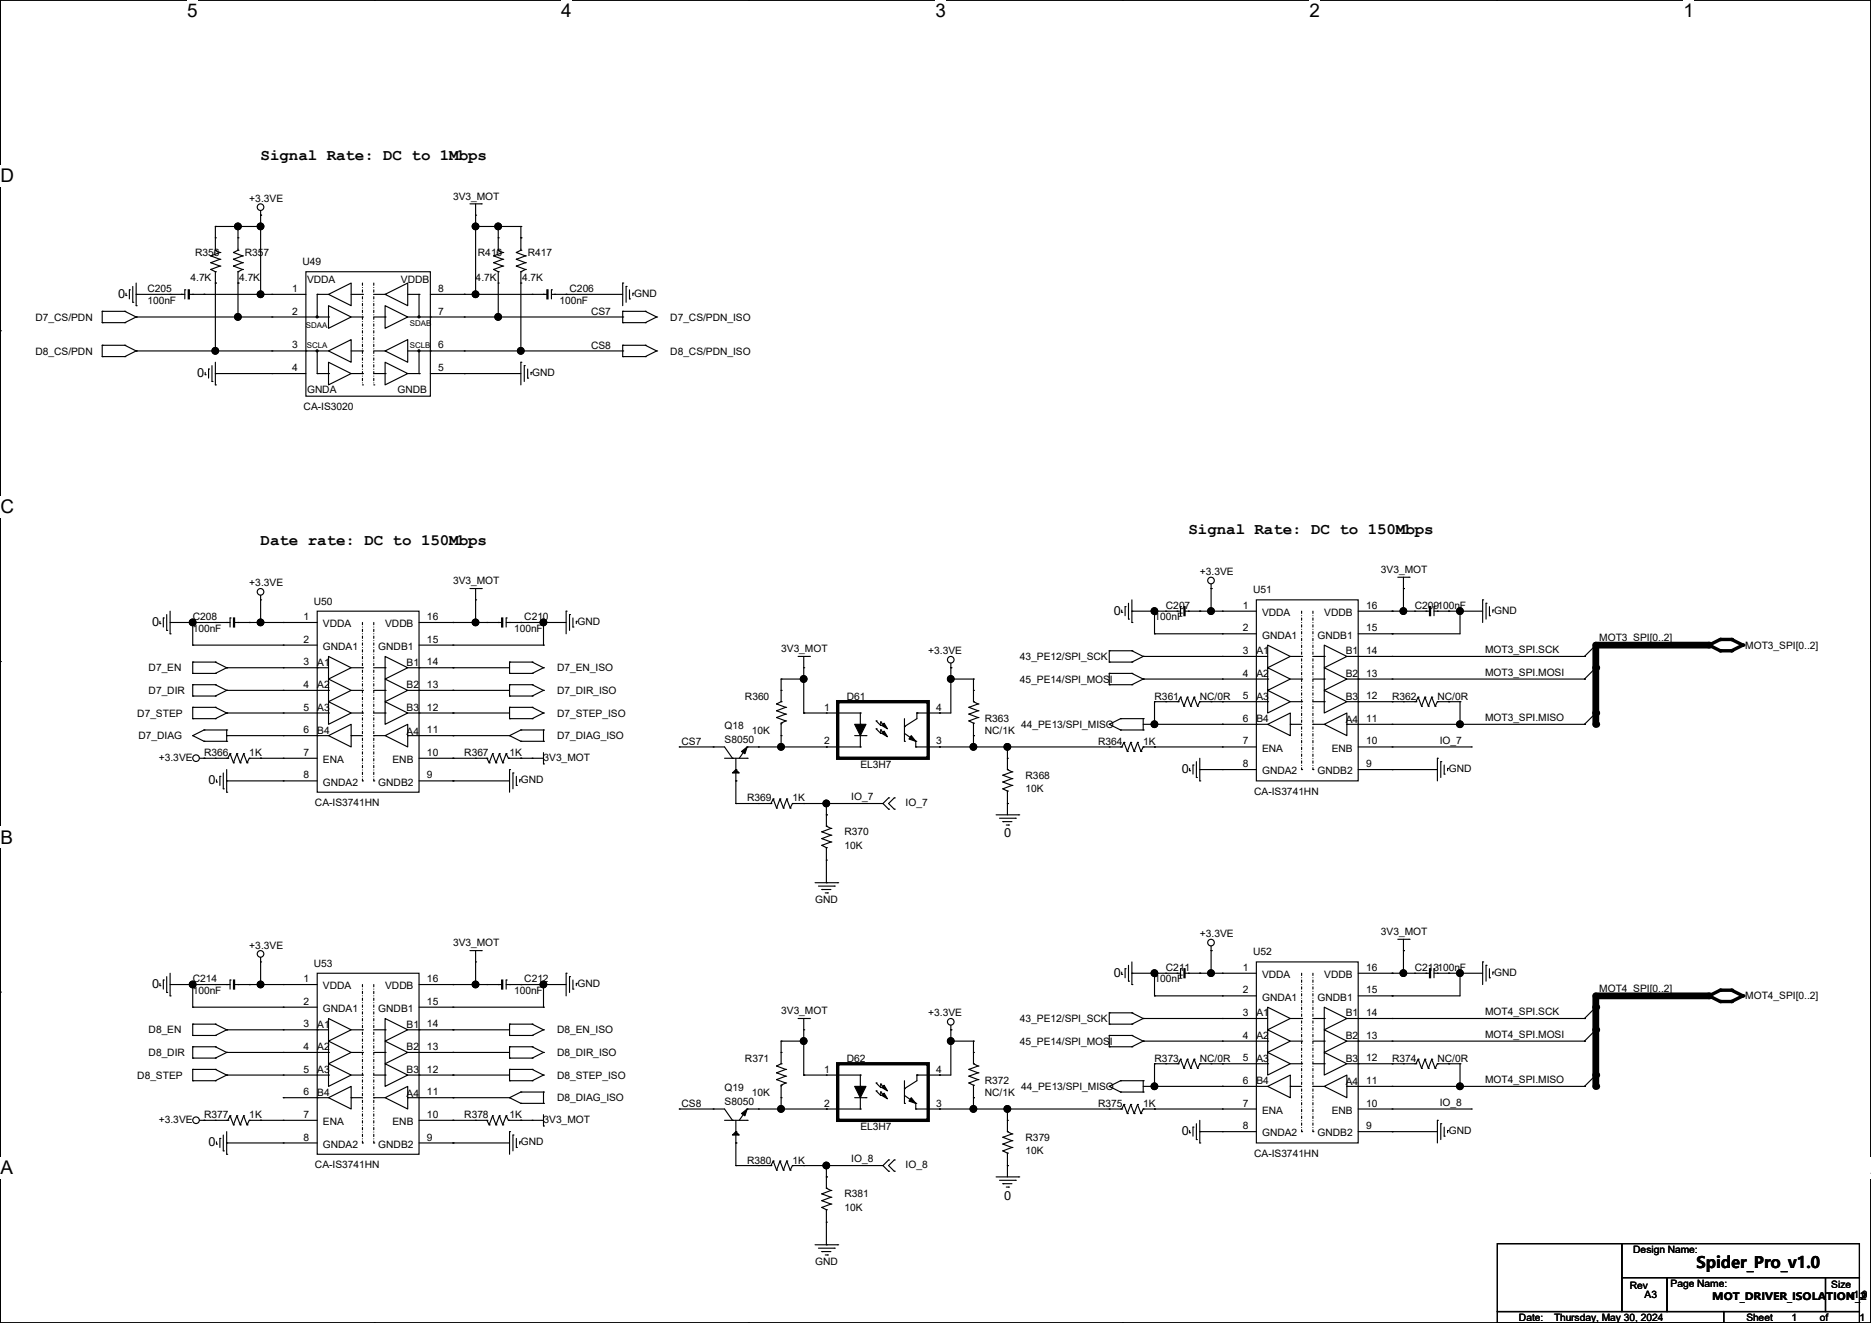
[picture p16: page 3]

Signal Rate: DC to 150Mbps Date rate: DC to 150Mbps

D D

## Signal Rate: DC to 1Mbps

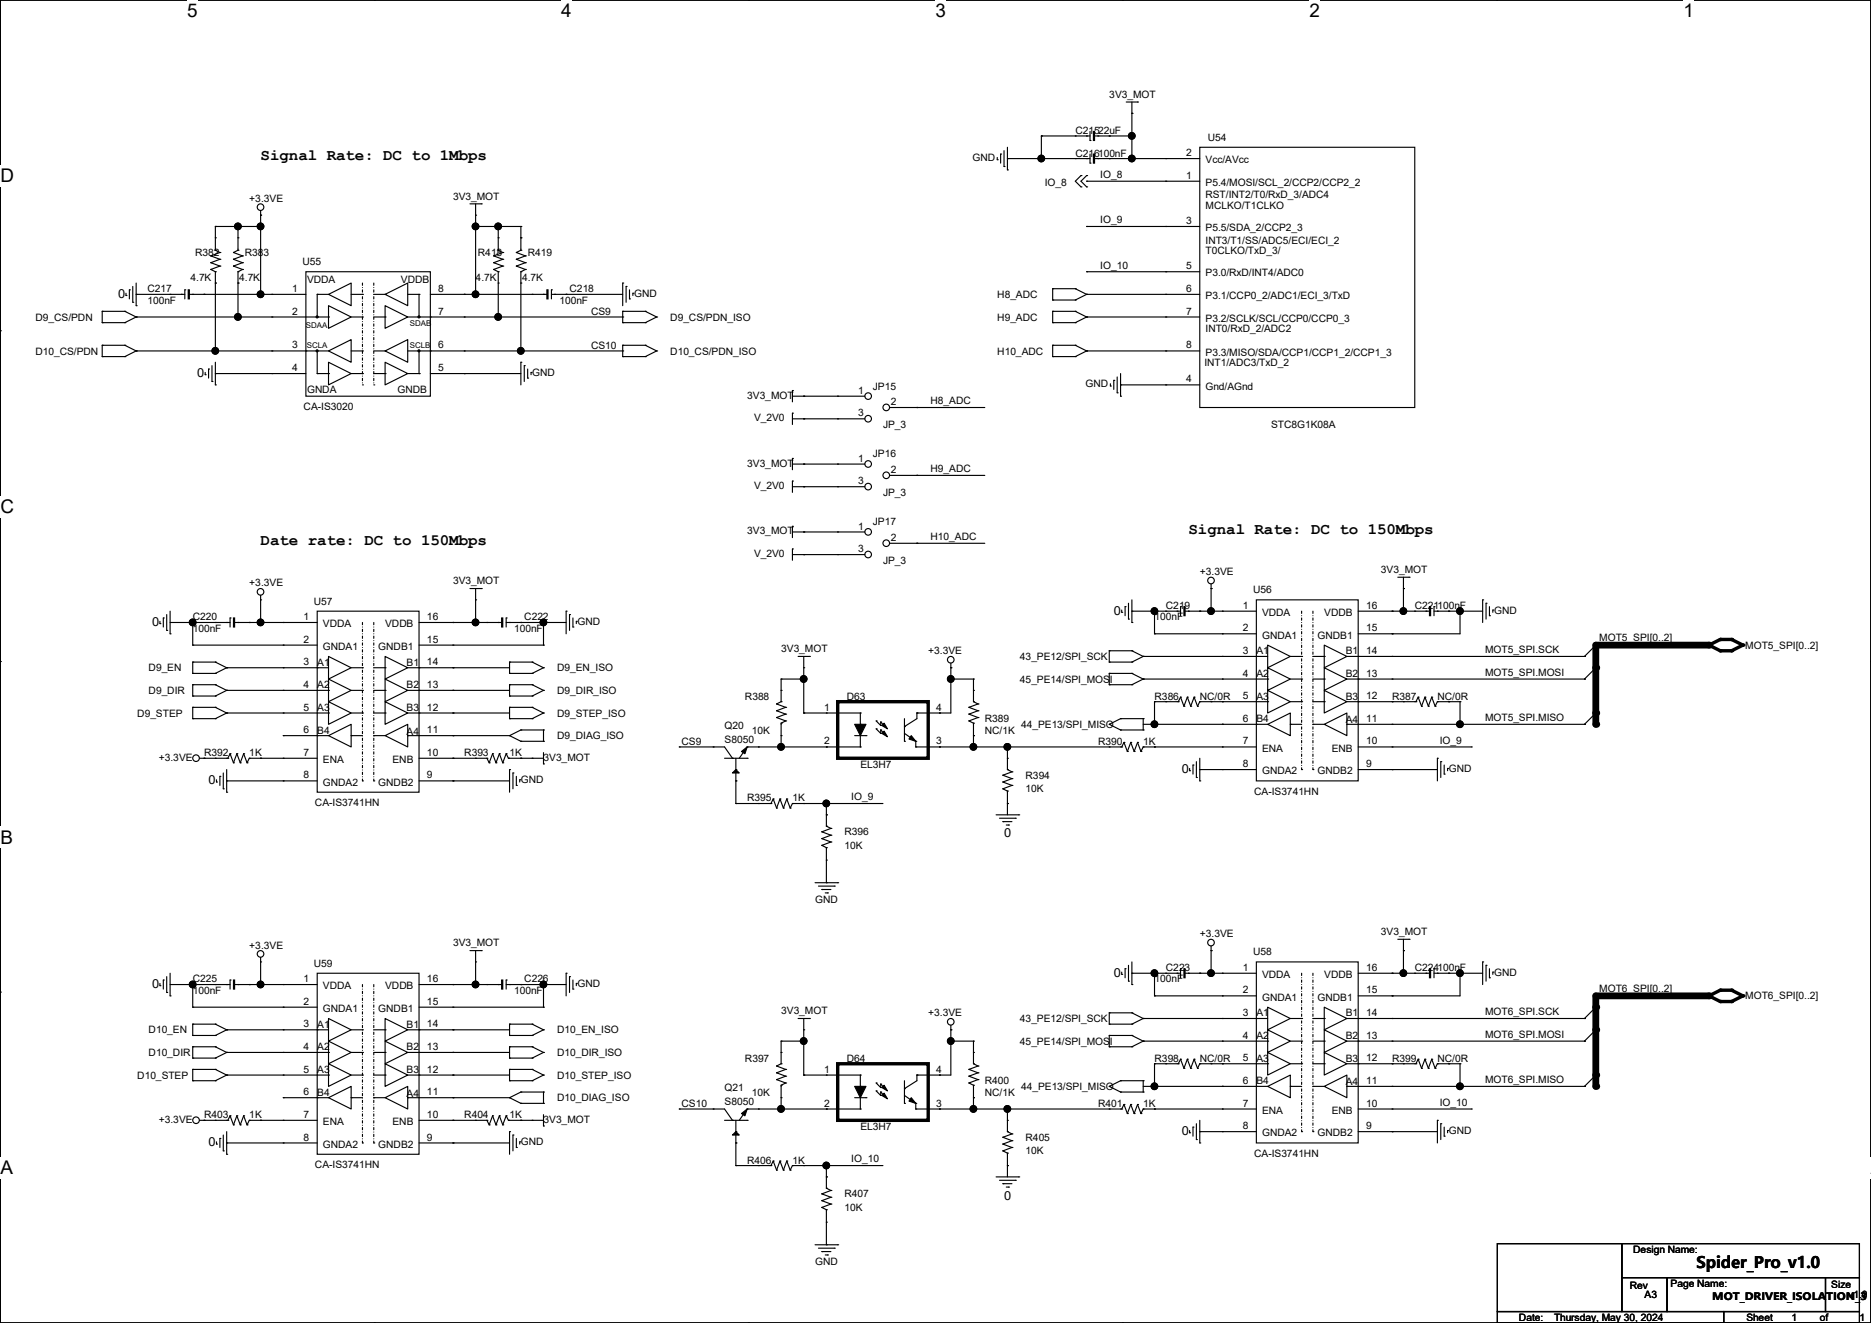
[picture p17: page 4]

Signal Rate: DC to 150Mbps Date rate: DC to 150Mbps

D D

## Signal Rate: DC to 1Mbps

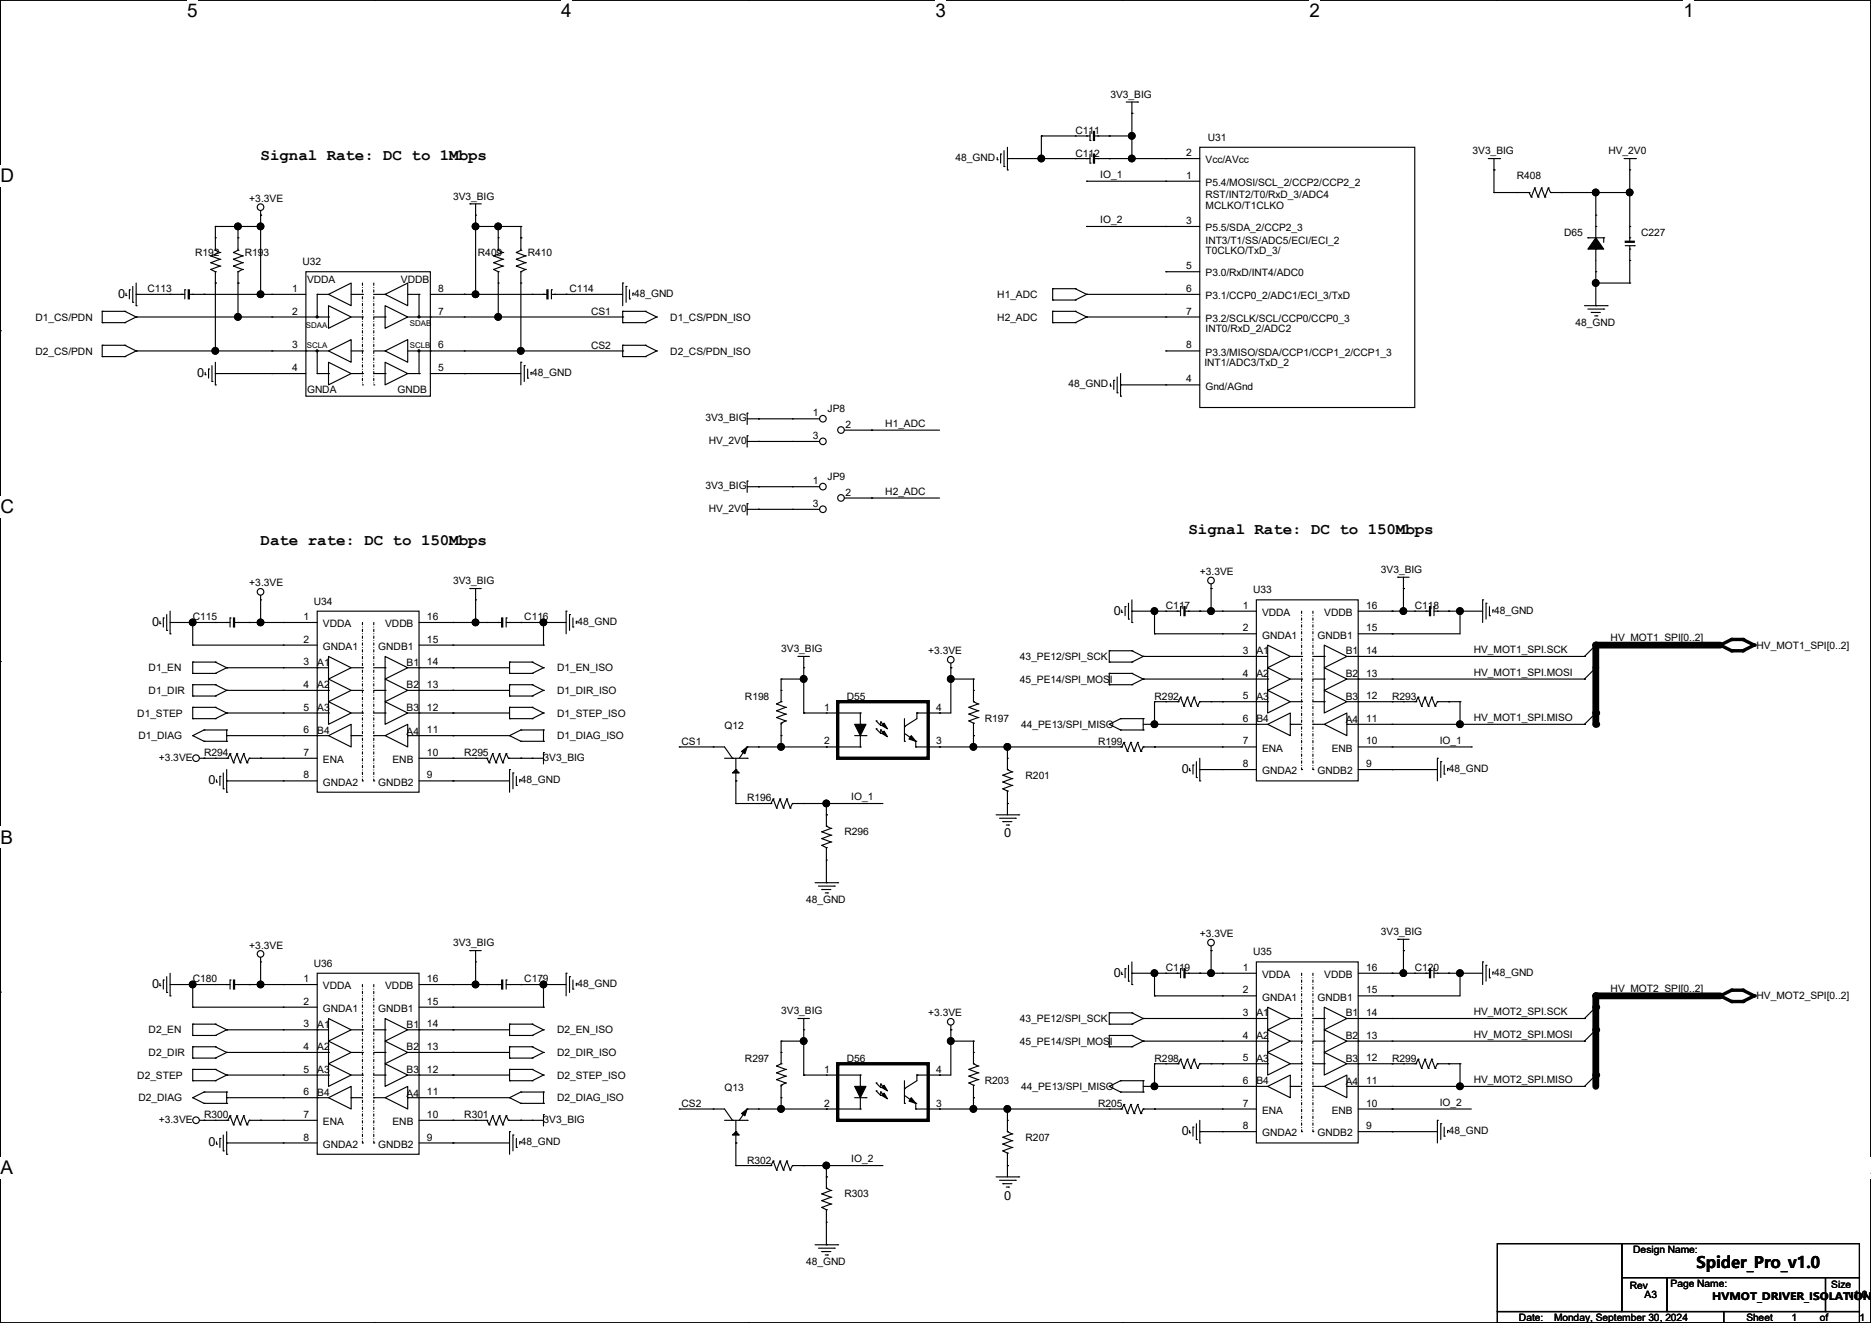
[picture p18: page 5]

Signal Rate: DC to 150Mbps Date rate: DC to 150Mbps

D D

## Signal Rate: DC to 1Mbps

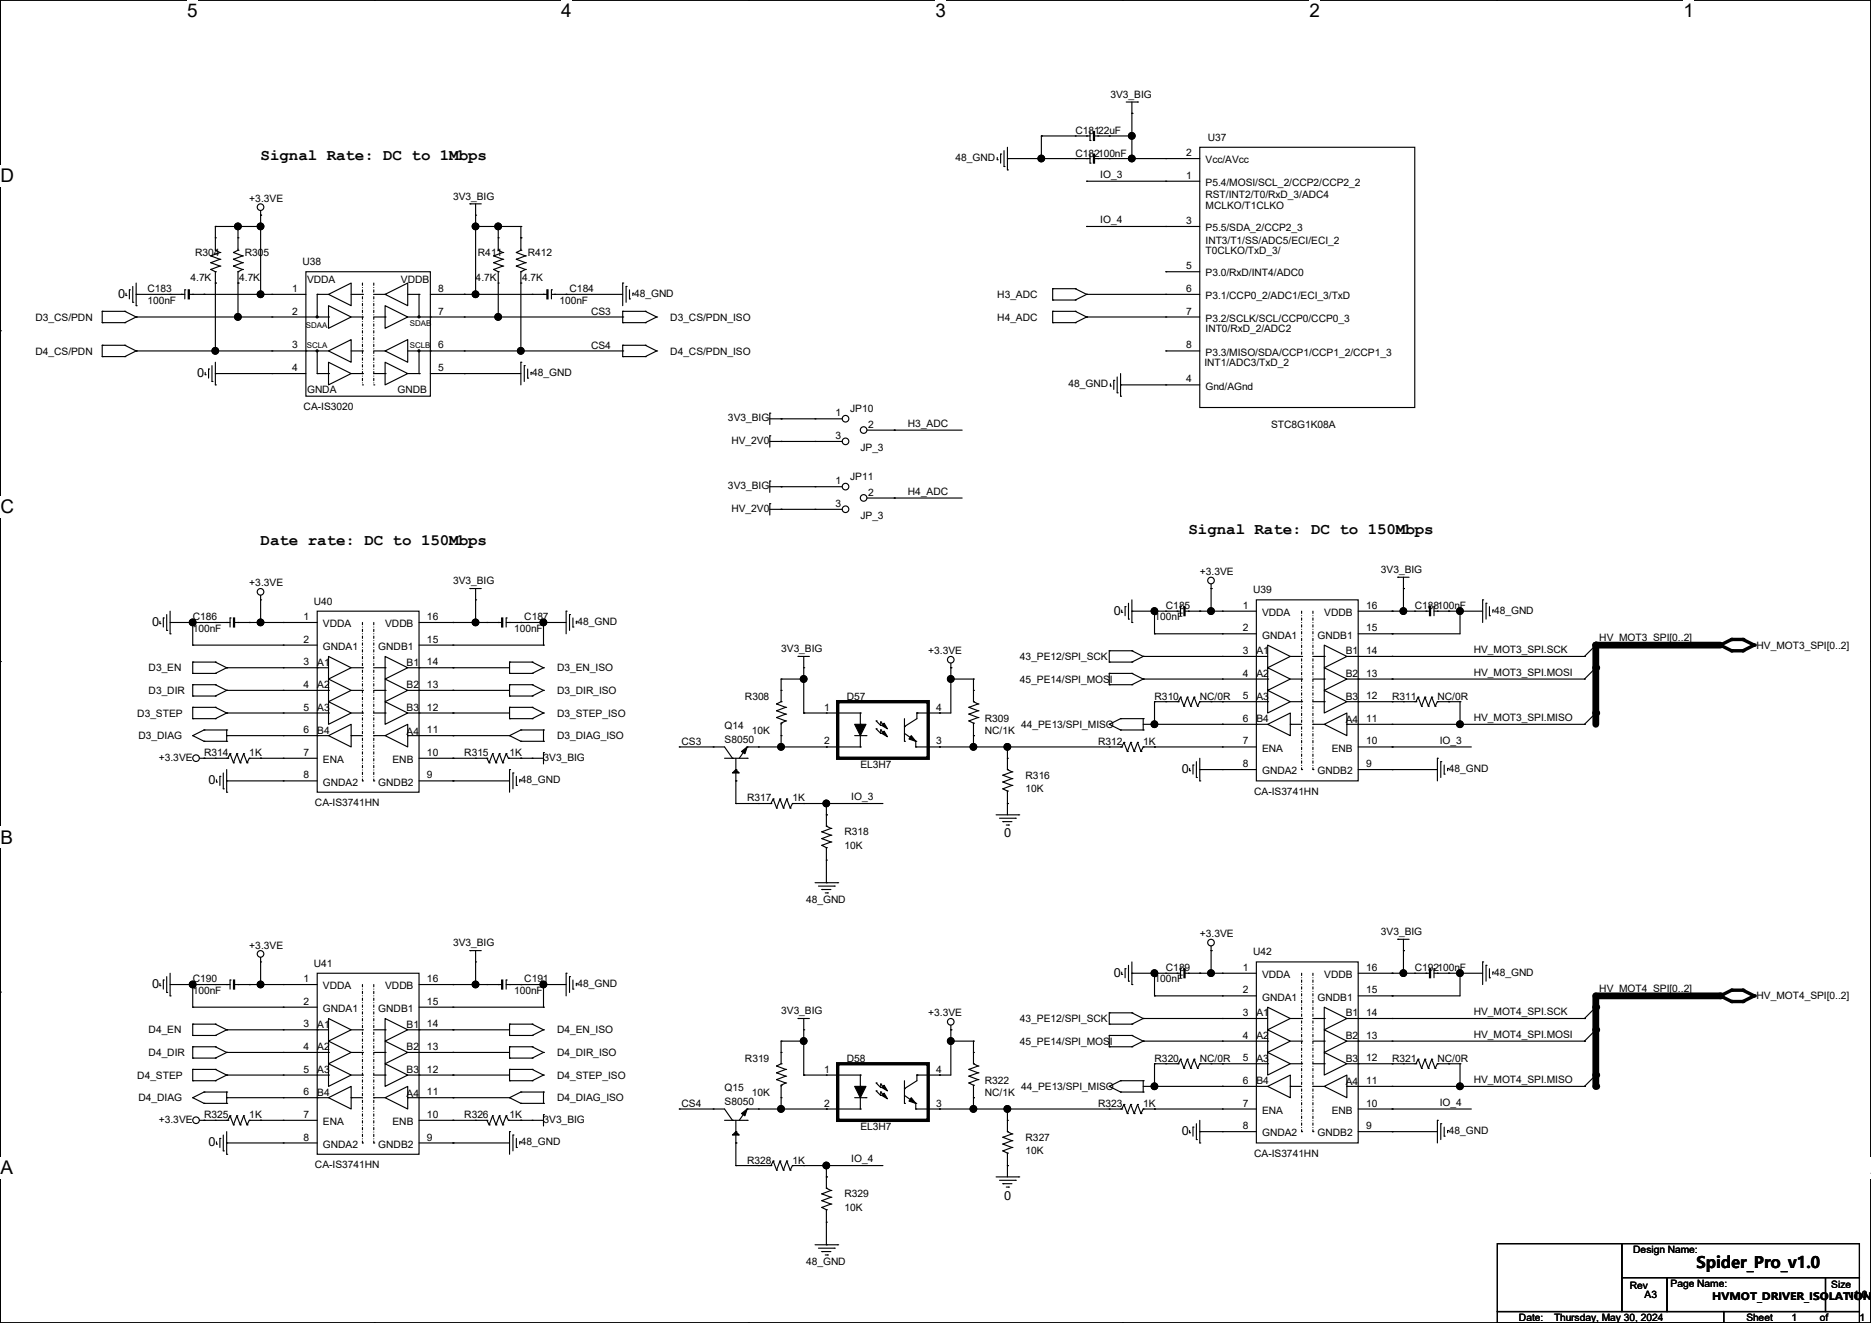
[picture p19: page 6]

Signal Rate: DC to 150Mbps Date rate: DC to 150Mbps

D D

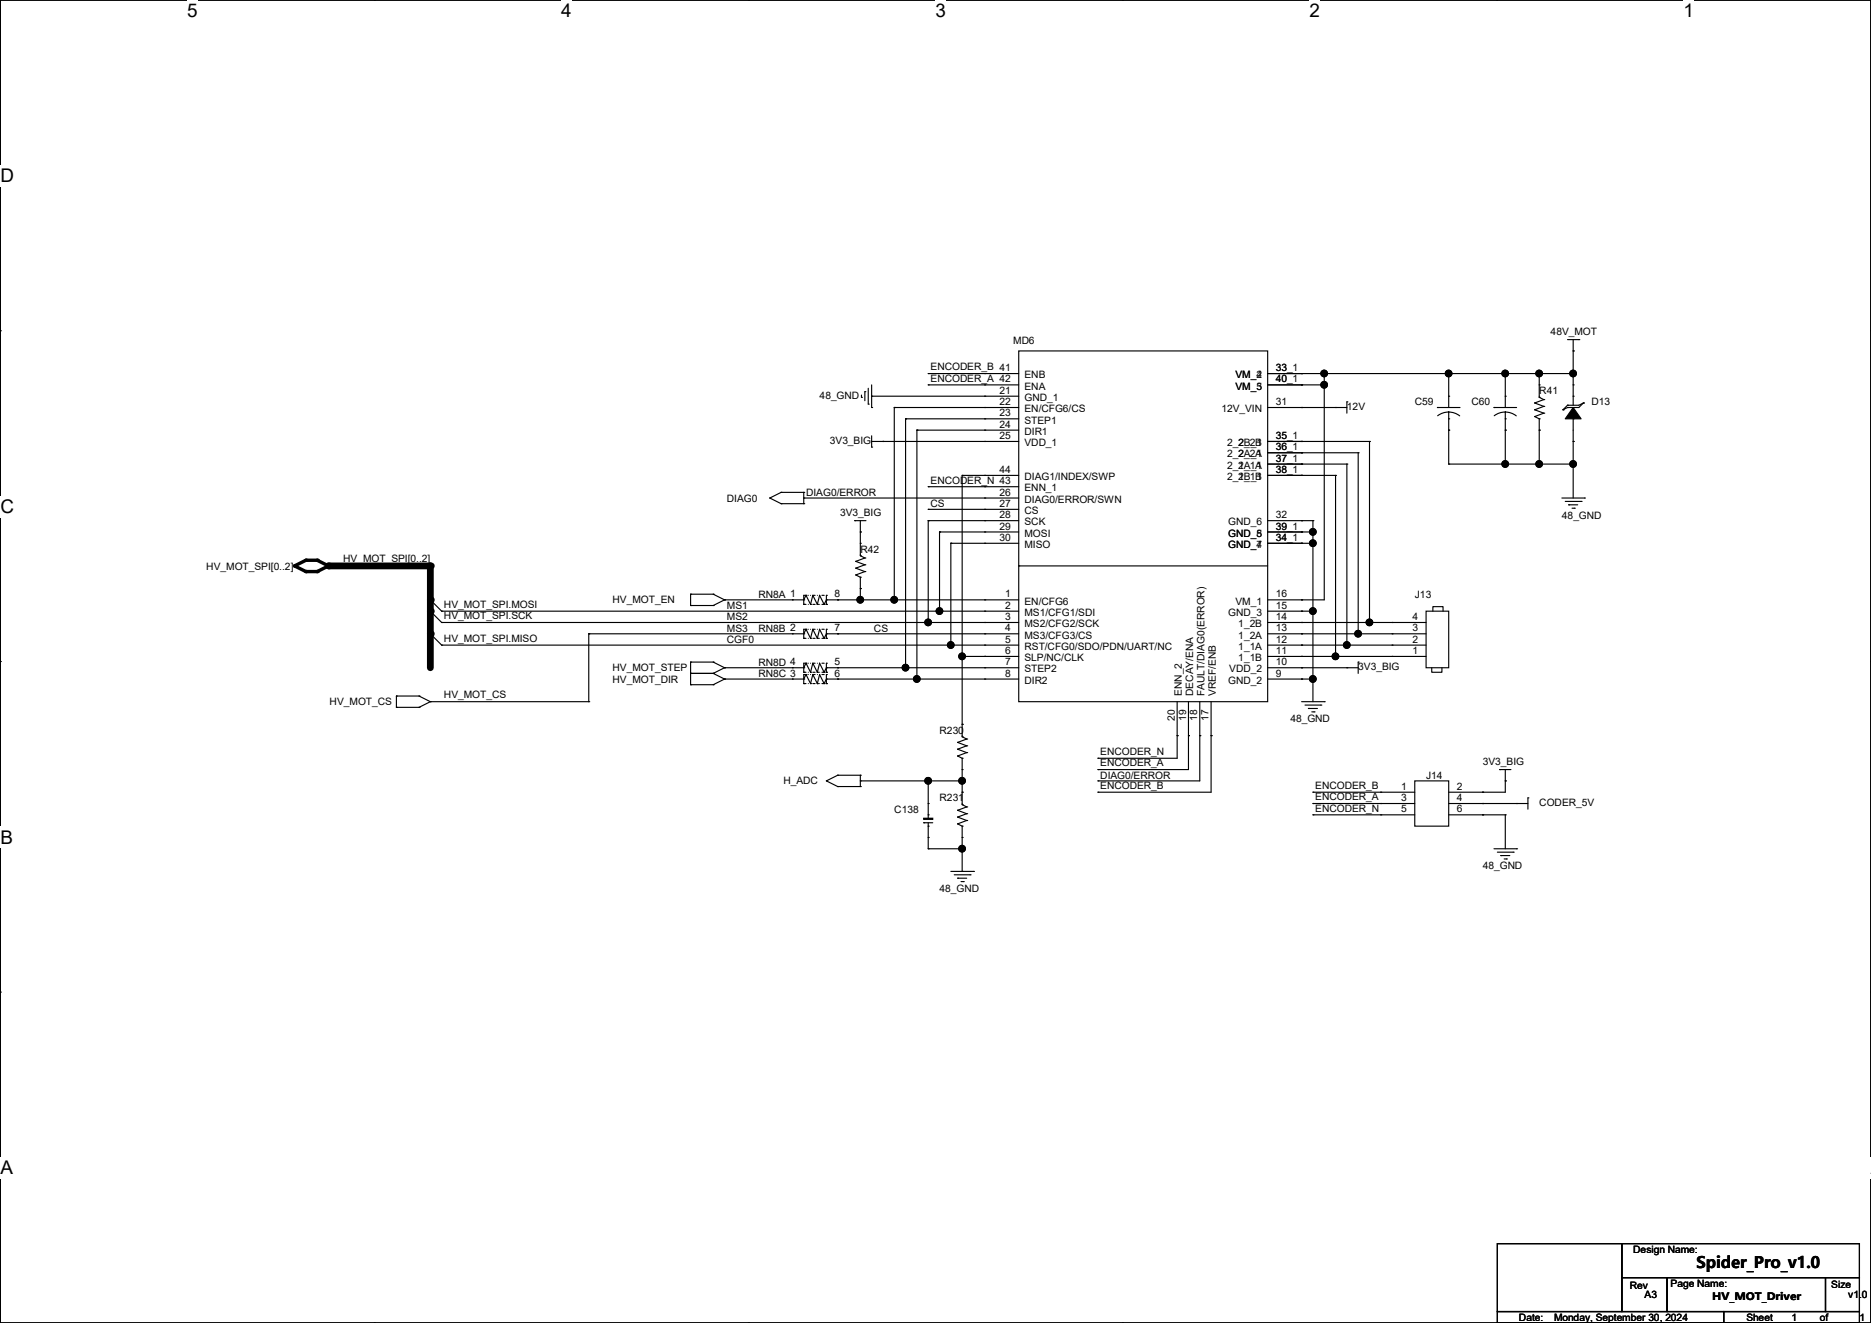
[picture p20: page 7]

D D

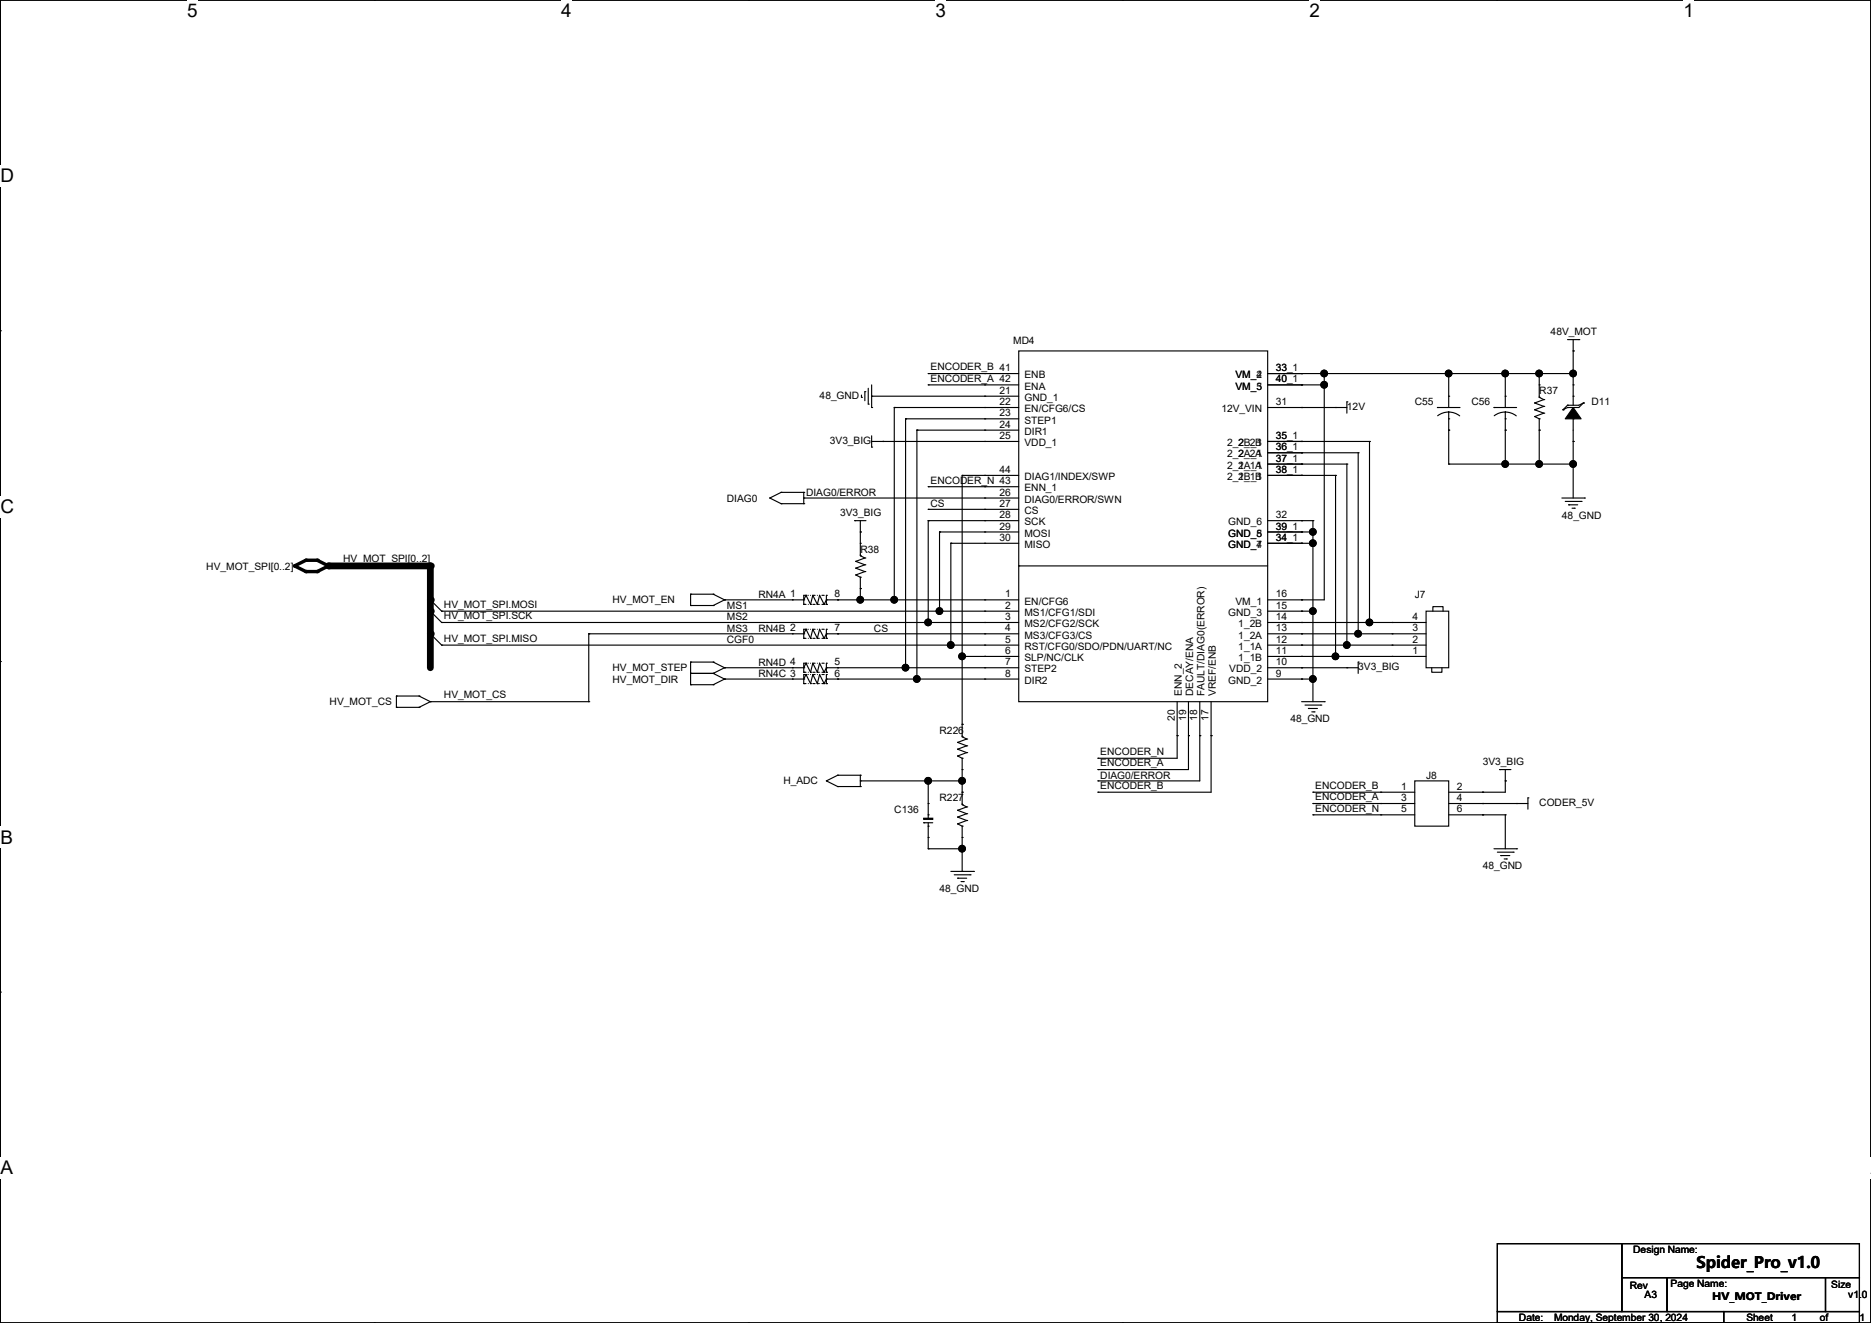
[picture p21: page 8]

D D


D D


D D


0



150Kbps Quad-Channel Digital Isolators




0

D6_DIAG LCD_RS LCD_D4 LCD_D5 LCD_EN PROBE D1_CS/PDN D4_STEP D4_EN D4_DIR D4_CS/PDN D7_EN D10_CS/PDN D7_STEP FAN1 FAN0 ESP_RST IO_IN3 IO_IN2 ESP_TFR_RDY; CAN_RX CAN_TX D8_DIR D8_STEP D6_EN; BTN_EN2 ESP_EN BEEP BTN_ENC PI_RXD D7_DIAG; PI_TXD BL_PWM BTN_EN1 Neo-pixel D7_DIR N_OUT4 D6_STEP BED_OUT D6_DIR N_OUT3 D5_STEP D5_EN D5_DIR ESP_DATA_RDY D9_CS/PDN D9_STEP D9_DIR D9_EN; D6_CS/PDN D5_CS/PDN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

AGND B1 AVDD B2 PA2 B3 PA1 B4 PA0 B5 PC3 B6 PC2 B7 PC1 B8 PC0 B9 NRST B10 PF10 B11 PF9 B12 PF8 B13 PF7 B14 PF6 B15 PG6 B16 PG5 B17 PG4 B18 PG3 B19 PG2 B20 PD15 B21 PD14 B22 PD13 B23 PD12 B24 PD11 B25 PD10 B26 PD9 B27 PB14 B28 PB15 B29 PD8 B30

## SYS (Power)


如果电源模块品牌是 金升阳，则电阻是：140K;
如果电源模块品牌是 Hi-Link，则电阻是：51K;







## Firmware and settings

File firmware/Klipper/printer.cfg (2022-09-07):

## Voron Design VORON2 250/300/350mm Spider TMC2209 UART config

## *** THINGS TO CHANGE/CHECK: ***
## MCU paths                           [mcu] section
## Thermistor types                    [extruder] and [heater_bed] sections - See https://www.klipper3d.org/Config_Reference.html#common-thermistors for common thermistor types
## Bed sensor_pin                      [heater_bed] section
## Fan pins                            [heater_fan hotend_fan] amd [fan] sections
## Z Endstop Switch location           [safe_z_home] section
## Homing end position                 [gcode_macro G32] section
## Z Endstop Switch  offset for Z0     [stepper_z] section
## Probe points                        [quad_gantry_level] section
## Min & Max gantry corner postions    [quad_gantry_level] section
## PID tune                            [extruder] and [heater_bed] sections
## Fine tune E steps                   [extruder] section
[include mainsail.cfg]
#[include adxl.cfg]
[include z_calibration.cfg]

[mcu]
## Uncomment below if you're using the Raspberry uart0 to communicate with Spider-King
restart_method: command

##  You need to select 'Communication interface' to USB in 'make menuconfig'
##  when you compile Klipper for Spider
##	Obtain definition by "ls -l /dev/serial/by-id/" then unplug to verify
##--------------------------------------------------------------------
serial: /dev/serial/by-id/usb-Klipper_stm32f446xx_230032000851363131363530-if00
##	If you want to use the Raspberry uart0 to communicate with Spider, 
##  you need to select 'Communication interface' to 'Serial (on USART1 PA10/PA9)' 
##  in 'make menuconfig' when you compile klipper and set the serial as below
##--------------------------------------------------------------------
#serial: /dev/ttyAMA0
##--------------------------------------------------------------------

[printer]
kinematics: corexy
max_velocity: 300  
max_accel: 3000                 #Max 4000
max_z_velocity: 15          #Max 15 for 12V TMC Drivers, can increase for 24V
max_z_accel: 350
square_corner_velocity: 5.0

#####################################################################
#      X/Y Stepper Settings
#####################################################################

[stepper_x]
##  Connected to MOT1 (B Motor)
step_pin: PG7
dir_pin: PG6
enable_pin: !PE11
rotation_distance: 40
microsteps: 32
full_steps_per_rotation:200  #set to 400 for 0.9 degree stepper
endstop_pin: ^PC5 # IO-0
position_min: 0

##--------------------------------------------------------------------

##  Uncomment below for 250mm build
#position_endstop: 250
#position_max: 250

##  Uncomment for 300mm build
#position_endstop: 300
#position_max: 300

##  Uncomment for 350mm build
position_endstop: 350
position_max: 350

##--------------------------------------------------------------------
homing_speed: 50   #Max 100
homing_retract_dist: 5
homing_positive_dir: true

##  Make sure to update below for your relevant driver (2208 or 2209)
[tmc2209 stepper_x]
uart_pin: PD2
interpolate: False
run_current: 0.8
sense_resistor: 0.110
stealthchop_threshold: 0

[stepper_y]
##  Connected to MOT2 (A Motor)
step_pin: PG14
dir_pin: PG12
enable_pin: !PG15
rotation_distance: 40
microsteps: 32
full_steps_per_rotation:200  #set to 400 for 0.9 degree stepper
endstop_pin: PC4
position_min: 0
##--------------------------------------------------------------------

##  Uncomment for 250mm build
#position_endstop: 250
#position_max: 250

##  Uncomment for 300mm build
#position_endstop: 300
#position_max: 300

##  Uncomment for 350mm build
position_endstop: 350
position_max: 350

##--------------------------------------------------------------------
homing_speed: 50  #Max 100
homing_retract_dist: 5
homing_positive_dir: true

##  Make sure to update below for your relevant driver (2208 or 2209)
[tmc2209 stepper_y]
uart_pin: PD8
interpolate: False
run_current: 0.8
sense_resistor: 0.110
stealthchop_threshold: 0

#####################################################################
#   Z Stepper Settings
#####################################################################

## In MOT5 Position
## Z0 Stepper - Front Left
[stepper_z]
step_pin: PE5
dir_pin: PC13
enable_pin: !PE6
rotation_distance: 40
gear_ratio: 80:16
microsteps: 32
##  In IO-2 Position
endstop_pin: ^PB6
##  Z-position of nozzle (in mm) to z-endstop trigger point relative to print surface (Z0)
##  (+) value = endstop above Z0, (-) value = endstop below
##  Increasing position_endstop brings nozzle closer to the bed
##  After you run Z_ENDSTOP_CALIBRATE, position_endstop will be stored at the very end of your config
position_endstop: -0.5
##--------------------------------------------------------------------

##  Uncomment below for 250mm build
#position_max: 210

##  Uncomment below for 300mm build
#position_max: 260

##  Uncomment below for 350mm build
position_max: 310

##--------------------------------------------------------------------
position_min: -10
homing_speed: 8
second_homing_speed: 3
homing_retract_dist: 3

##  Make sure to update below for your relevant driver (2208 or 2209)
[tmc2209 stepper_z]
uart_pin: PC14
interpolate: False
run_current: 0.8
sense_resistor: 0.110
stealthchop_threshold: 0

##  In MOT6 Position
##  Z1 Stepper - Rear Left
[stepper_z1]
step_pin: PE3
dir_pin: !PE4
enable_pin: !PE2
rotation_distance: 40
gear_ratio: 80:16
microsteps: 32

##  Make sure to update below for your relevant driver (2208 or 2209)
[tmc2209 stepper_z1]
uart_pin: PC15
interpolate: False
run_current: 0.8
sense_resistor: 0.110
stealthchop_threshold: 0

##  In MOT10 Position
##  Z2 Stepper - Rear Right
[stepper_z2]
step_pin: PF15
dir_pin: PG0
enable_pin: !PG5
rotation_distance: 40
gear_ratio: 80:16
microsteps: 32

##  Make sure to update below for your relevant driver (2208 or 2209)
[tmc2209 stepper_z2]
uart_pin: PG11
interpolate: False
run_current: 0.8
sense_resistor: 0.110
stealthchop_threshold: 0

##  In MOT8 Position
##  Z3 Stepper - Front Right
[stepper_z3]
step_pin: PE1
dir_pin: !PE0
enable_pin: !PB2
rotation_distance: 40
gear_ratio: 80:16
microsteps: 32

[tmc2209 stepper_z3]
uart_pin: PD9
interpolate: False
run_current: 0.8
sense_resistor: 0.110
stealthchop_threshold: 0

#####################################################################
#   Extruder
#####################################################################

##  In MOT9 Position
[extruder]
step_pin: PF4
dir_pin: PF3
enable_pin: !PF2

##  Update value below when you perform extruder calibration
##  If you ask for 100mm of filament, but in reality it is 98mm:
##  rotation_distance = <previous_rotation_distance> * <actual_extrude_distance> / 100
##  22.6789511 is a good starting point for Bondtech 5mm gears
##  34.37086 for Bondtech 8mm gears (Galileo)
rotation_distance: 22.6789511   #Bondtech 5mm Drive Gears
##  Update Gear Ratio depending on your Extruder Type
##  Use 50:17 for Afterburner/Clockwork (BMG Gear Ratio)
##  Use 80:20 for M4, M3.1
##  Use 7.5:1 for Galileo
gear_ratio: 50:17               #BMG Gear Ratio
microsteps: 32
full_steps_per_rotation: 200    #200 for 1.8 degree, 400 for 0.9 degree
nozzle_diameter: 0.400
filament_diameter: 1.75
##      In OUT0 Position
heater_pin: PB4
## Check what thermistor type you have. See https://www.klipper3d.org/Config_Reference.html#common-thermistors for common thermistor types.
## Use "Generic 3950" for NTC 100k 3950 thermistors
sensor_type: Generic 3950
sensor_pin: PC1 # T0 position
min_temp: 10
max_temp: 270
max_power: 1.0
min_extrude_temp: 170
control = pid
pid_kp = 26.213
pid_ki = 1.304
pid_kd = 131.721
##  Try to keep pressure_advance below 1.0
#pressure_advance: 0.05
##  Default is 0.040, leave stock
#pressure_advance_smooth_time: 0.040

##  In MOT9 Position
##  Make sure to update below for your relevant driver (2208 or 2209)
[tmc2209 extruder]
uart_pin: PF5
interpolate: false
run_current: 0.5
sense_resistor: 0.110
stealthchop_threshold: 0

#####################################################################
#   Bed Heater
#####################################################################

[heater_bed]
##  SSR Pin - In BED OUT position
heater_pin: PE10
## Check what thermistor type you have. See https://www.klipper3d.org/Config_Reference.html#common-thermistors for common thermistor types.
## Use "Generic 3950" for Keenovo heaters
sensor_type: Generic 3950

##--------------------------------------------------------------------
##  Select the option that matches your board
#sensor_pin: PC3 # Spider 1.0 & 1.1
#sensor_pin: PB0 # Spider 2.2
sensor_pin: PF10 # Spider King
##--------------------------------------------------------------------

##  Adjust Max Power so your heater doesn't warp your bed
max_power: 0.6
min_temp: 0
max_temp: 120
control: pid
pid_kp: 58.437
pid_ki: 2.347
pid_kd: 363.769

#####################################################################
#   Probe
#####################################################################
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

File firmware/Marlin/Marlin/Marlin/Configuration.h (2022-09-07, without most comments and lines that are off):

#pragma once
#define CONFIGURATION_H_VERSION 02010100
#define STRING_CONFIG_H_AUTHOR "(none, default config)" // Who made the changes.
#define SHOW_BOOTSCREEN
  #define MOTHERBOARD BOARD_FYSETC_SPIDER_KING407
#define SERIAL_PORT 0
#define BAUDRATE 250000
#define X_DRIVER_TYPE  A4988
#define Y_DRIVER_TYPE  A4988
#define Z_DRIVER_TYPE  A4988
#define E0_DRIVER_TYPE A4988
#define EXTRUDERS 1
#define DEFAULT_NOMINAL_FILAMENT_DIA 1.75
#define TEMP_SENSOR_0 1
#define TEMP_SENSOR_1 0
#define TEMP_SENSOR_2 0
#define TEMP_SENSOR_3 0
#define TEMP_SENSOR_4 0
#define TEMP_SENSOR_5 0
#define TEMP_SENSOR_6 0
#define TEMP_SENSOR_7 0
#define TEMP_SENSOR_BED 0
#define TEMP_SENSOR_PROBE 0
#define TEMP_SENSOR_CHAMBER 0
#define TEMP_SENSOR_COOLER 0
#define TEMP_SENSOR_BOARD 0
#define TEMP_SENSOR_REDUNDANT 0
#define DUMMY_THERMISTOR_998_VALUE  25
#define DUMMY_THERMISTOR_999_VALUE 100
#if TEMP_SENSOR_IS_MAX_TC(0)
  #define MAX31865_SENSOR_OHMS_0      100 // (Ω) Typically 100 or 1000 (PT100 or PT1000)
  #define MAX31865_CALIBRATION_OHMS_0 430 // (Ω) Typically 430 for Adafruit PT100; 4300 for Adafruit PT1000
#endif
#if TEMP_SENSOR_IS_MAX_TC(1)
  #define MAX31865_SENSOR_OHMS_1      100
  #define MAX31865_CALIBRATION_OHMS_1 430
#endif
#if HAS_E_TEMP_SENSOR
  #define TEMP_RESIDENCY_TIME         10  // (seconds) Time to wait for hotend to "settle" in M109
  #define TEMP_WINDOW                  1  // (°C) Temperature proximity for the "temperature reached" timer
  #define TEMP_HYSTERESIS              3  // (°C) Temperature proximity considered "close enough" to the target
#endif
#if TEMP_SENSOR_BED
  #define TEMP_BED_RESIDENCY_TIME     10  // (seconds) Time to wait for bed to "settle" in M190
  #define TEMP_BED_WINDOW              1  // (°C) Temperature proximity for the "temperature reached" timer
  #define TEMP_BED_HYSTERESIS          3  // (°C) Temperature proximity considered "close enough" to the target
#endif
#if TEMP_SENSOR_CHAMBER
  #define TEMP_CHAMBER_RESIDENCY_TIME 10  // (seconds) Time to wait for chamber to "settle" in M191
  #define TEMP_CHAMBER_WINDOW          1  // (°C) Temperature proximity for the "temperature reached" timer
  #define TEMP_CHAMBER_HYSTERESIS      3  // (°C) Temperature proximity considered "close enough" to the target
#endif
#if TEMP_SENSOR_REDUNDANT
  #define TEMP_SENSOR_REDUNDANT_SOURCE    E1  // The sensor that will provide the redundant reading.
  #define TEMP_SENSOR_REDUNDANT_TARGET    E0  // The sensor that we are providing a redundant reading for.
  #define TEMP_SENSOR_REDUNDANT_MAX_DIFF  10  // (°C) Temperature difference that will trigger a print abort.
#endif
#define HEATER_0_MINTEMP   5
#define HEATER_1_MINTEMP   5
#define HEATER_2_MINTEMP   5
#define HEATER_3_MINTEMP   5
#define HEATER_4_MINTEMP   5
#define HEATER_5_MINTEMP   5
#define HEATER_6_MINTEMP   5
#define HEATER_7_MINTEMP   5
#define BED_MINTEMP        5
#define CHAMBER_MINTEMP    5
#define HEATER_0_MAXTEMP 275
#define HEATER_1_MAXTEMP 275
#define HEATER_2_MAXTEMP 275
#define HEATER_3_MAXTEMP 275
#define HEATER_4_MAXTEMP 275
#define HEATER_5_MAXTEMP 275
#define HEATER_6_MAXTEMP 275
#define HEATER_7_MAXTEMP 275
#define BED_MAXTEMP      150
#define CHAMBER_MAXTEMP  60
#define HOTEND_OVERSHOOT 15   // (°C) Forbid temperatures over MAXTEMP - OVERSHOOT
#define BED_OVERSHOOT    10   // (°C) Forbid temperatures over MAXTEMP - OVERSHOOT
#define COOLER_OVERSHOOT  2   // (°C) Forbid temperatures closer than OVERSHOOT
#define PIDTEMP          // See the PID Tuning Guide at https://reprap.org/wiki/PID_Tuning
#define BANG_MAX 255     // Limits current to nozzle while in bang-bang mode; 255=full current
#define PID_MAX BANG_MAX // Limits current to nozzle while PID is active (see PID_FUNCTIONAL_RANGE below); 255=full current
#define PID_K1 0.95      // Smoothing factor within any PID loop
    #define DEFAULT_Kp  22.20
    #define DEFAULT_Ki   1.08
    #define DEFAULT_Kd 114.00
#define MAX_BED_POWER 255 // limits duty cycle to bed; 255=full current
#define MAX_CHAMBER_POWER 255 // limits duty cycle to chamber heater; 255=full current
  #define PID_FUNCTIONAL_RANGE 10 // If the temperature difference between the target temperature and the actual temperature
#define PREVENT_COLD_EXTRUSION
#define EXTRUDE_MINTEMP 170
#define PREVENT_LENGTHY_EXTRUDE
#define EXTRUDE_MAXLENGTH 200
#define THERMAL_PROTECTION_HOTENDS // Enable thermal protection for all extruders
#define THERMAL_PROTECTION_BED     // Enable thermal protection for the heated bed
#define THERMAL_PROTECTION_CHAMBER // Enable thermal protection for the heated chamber
#define THERMAL_PROTECTION_COOLER  // Enable thermal protection for the laser cooling
#define USE_XMIN_PLUG
#define USE_YMIN_PLUG
#define USE_ZMIN_PLUG
#define ENDSTOPPULLUPS
#define X_MIN_ENDSTOP_INVERTING false // Set to true to invert the logic of the endstop.
#define Y_MIN_ENDSTOP_INVERTING false // Set to true to invert the logic of the endstop.
#define Z_MIN_ENDSTOP_INVERTING false // Set to true to invert the logic of the endstop.
#define I_MIN_ENDSTOP_INVERTING false // Set to true to invert the logic of the endstop.
#define J_MIN_ENDSTOP_INVERTING false // Set to true to invert the logic of the endstop.
#define K_MIN_ENDSTOP_INVERTING false // Set to true to invert the logic of the endstop.
#define U_MIN_ENDSTOP_INVERTING false // Set to true to invert the logic of the endstop.
#define V_MIN_ENDSTOP_INVERTING false // Set to true to invert the logic of the endstop.
#define W_MIN_ENDSTOP_INVERTING false // Set to true to invert the logic of the endstop.
#define X_MAX_ENDSTOP_INVERTING false // Set to true to invert the logic of the endstop.
#define Y_MAX_ENDSTOP_INVERTING false // Set to true to invert the logic of the endstop.
#define Z_MAX_ENDSTOP_INVERTING false // Set to true to invert the logic of the endstop.
#define I_MAX_ENDSTOP_INVERTING false // Set to true to invert the logic of the endstop.
#define J_MAX_ENDSTOP_INVERTING false // Set to true to invert the logic of the endstop.
#define K_MAX_ENDSTOP_INVERTING false // Set to true to invert the logic of the endstop.
#define U_MAX_ENDSTOP_INVERTING false // Set to true to invert the logic of the endstop.
#define V_MAX_ENDSTOP_INVERTING false // Set to true to invert the logic of the endstop.
#define W_MAX_ENDSTOP_INVERTING false // Set to true to invert the logic of the endstop.
#define Z_MIN_PROBE_ENDSTOP_INVERTING false // Set to true to invert the logic of the probe.
#define DEFAULT_AXIS_STEPS_PER_UNIT   { 80, 80, 400, 500 }
#define DEFAULT_MAX_FEEDRATE          { 300, 300, 5, 25 }
#define DEFAULT_MAX_ACCELERATION      { 3000, 3000, 100, 10000 }
#define DEFAULT_ACCELERATION          3000    // X, Y, Z and E acceleration for printing moves
#define DEFAULT_RETRACT_ACCELERATION  3000    // E acceleration for retracts
#define DEFAULT_TRAVEL_ACCELERATION   3000    // X, Y, Z acceleration for travel (non printing) moves
#define DEFAULT_EJERK    5.0  // May be used by Linear Advance
  #define JUNCTION_DEVIATION_MM 0.013 // (mm) Distance from real junction edge
  #define JD_HANDLE_SMALL_SEGMENTS    // Use curvature estimation instead of just the junction angle
#define Z_MIN_PROBE_USES_Z_MIN_ENDSTOP_PIN
#define NOZZLE_TO_PROBE_OFFSET { 10, 10, 0 }
#define PROBING_MARGIN 10
#define XY_PROBE_FEEDRATE (133*60)
#define Z_PROBE_FEEDRATE_FAST (4*60)
#define Z_PROBE_FEEDRATE_SLOW (Z_PROBE_FEEDRATE_FAST / 2)
#define Z_CLEARANCE_DEPLOY_PROBE   10 // Z Clearance for Deploy/Stow
#define Z_CLEARANCE_BETWEEN_PROBES  5 // Z Clearance between probe points
#define Z_CLEARANCE_MULTI_PROBE     5 // Z Clearance between multiple probes
#define Z_PROBE_LOW_POINT          -2 // Farthest distance below the trigger-point to go before stopping
#define Z_PROBE_OFFSET_RANGE_MIN -20
#define Z_PROBE_OFFSET_RANGE_MAX 20
#define X_ENABLE_ON 0
#define Y_ENABLE_ON 0
#define Z_ENABLE_ON 0
#define E_ENABLE_ON 0 // For all extruders
#define DISABLE_X false
#define DISABLE_Y false
#define DISABLE_Z false
#define DISABLE_E false             // Disable the extruder when not stepping
#define DISABLE_INACTIVE_EXTRUDER   // Keep only the active extruder enabled
#define INVERT_X_DIR false
#define INVERT_Y_DIR true
#define INVERT_Z_DIR false
#define INVERT_E0_DIR false
#define INVERT_E1_DIR false
#define INVERT_E2_DIR false
#define INVERT_E3_DIR false
#define INVERT_E4_DIR false
#define INVERT_E5_DIR false
#define INVERT_E6_DIR false
#define INVERT_E7_DIR false
#define X_HOME_DIR -1
#define Y_HOME_DIR -1
#define Z_HOME_DIR -1
#define X_BED_SIZE 200
#define Y_BED_SIZE 200
#define X_MIN_POS 0
#define Y_MIN_POS 0
#define Z_MIN_POS 0
#define X_MAX_POS X_BED_SIZE
#define Y_MAX_POS Y_BED_SIZE
#define Z_MAX_POS 200
#define MIN_SOFTWARE_ENDSTOPS
  #define MIN_SOFTWARE_ENDSTOP_X
  #define MIN_SOFTWARE_ENDSTOP_Y
  #define MIN_SOFTWARE_ENDSTOP_Z
  #define MIN_SOFTWARE_ENDSTOP_I
  #define MIN_SOFTWARE_ENDSTOP_J
  #define MIN_SOFTWARE_ENDSTOP_K
  #define MIN_SOFTWARE_ENDSTOP_U
  #define MIN_SOFTWARE_ENDSTOP_V
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

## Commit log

2022-09-07 Upload Marlin
    [Configuration.h, Configuration_adv.h, esp32.csv]
2022-09-07 Upload Klipper
    [generic-spider-king407.cfg, printer.cfg, sample-lcd.cfg]
2022-09-09 Update config
    [generic-spider-king407.cfg]
2022-09-13 Add printer.cfg for vzbot machine
    [vzbot+Big5160_printer.cfg]
2022-10-13 Upload Board holder STLs
    [Holder_long_right.STL, Holder_short_left.STL]
2022-11-23 Upload silk and cad
    [Spider_King_CAD.dxf]
2024-09-30 Update
    Updated schematics, CAD, SILK
    [Spider_King v1.1_CAD.dxf]

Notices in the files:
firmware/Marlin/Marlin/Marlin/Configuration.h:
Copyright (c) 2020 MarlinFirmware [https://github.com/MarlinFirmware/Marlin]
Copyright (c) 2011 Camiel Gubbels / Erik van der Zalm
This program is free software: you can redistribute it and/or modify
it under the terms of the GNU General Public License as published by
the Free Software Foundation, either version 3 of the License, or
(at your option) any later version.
